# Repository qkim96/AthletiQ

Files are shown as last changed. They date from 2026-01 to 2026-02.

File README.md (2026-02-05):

# AthletiQ

## Table of Contents
<ul>
  <li>
    <a href="#project-overview">Project Overview</a>
  </li><br>

  <li>
    <a href="#methodology">Methodology</a>
    <ul>
      <li><a href="#object-detection">Object Detection</a></li>
      <li><a href="#object-tracking">Object Tracking</a></li>
      <li><a href="#pose-detection">Pose Detection</a></li>
      <li><a href="#action-state-estimation">Action State Estimation</a></li>
      <li><a href="#camera-orientation--control">Camera Orientation & Control</a></li>
      <li><a href="#data-transmission">Data Transmission</a></li>
    </ul>
  </li><br>

  <li>
    <a href="#system-design">System Design</a>
    <ul>
      <li><a href="#hardware">Hardware</a></li>
      <li><a href="#functionality">Functionality</a></li>
      <li><a href="#communication">Communication</a></li>
    </ul>
  </li><br>

  <li>
    <a href="#installation--configuration">Installation & Configuration</a>
    <ul>
      <li><a href="#tested-environments">Tested Environments</a></li>
      <li><a href="#prerequisites">Prerequisites</a></li>
      <li><a href="#structure">Structure</a></li>
      <li><a href="#setup-raspberry-pi">Setup (Raspberry Pi)</a></li>
      <li><a href="#setup-mobile-device">Setup (Mobile Device)</a></li>
    </ul>
  </li><br>

  <li>
    <a href="#operating-instructions">Operating Instructions</a>
    <ul>
      <li><a href="#hardware-1">Hardware</a></li>
      <li><a href="#mobile-device">Mobile Device</a></li>
    </ul>
  </li>
</ul>

<br><br>

---

## Project Overview
This project implements an autonomous, real-time basketball shooting capture and analysis system.

A motorized camera mounted on stationary device continuously tracks a player on the court, keeping the athlete centered in the frame during the play.
The system processes a live video feed to detect shooting events and automatically triggers recording when a shot occurs.
Each captured clip includes both the shooting action and a short temporal window preceding the event.
The system then analyzes the clip to extract the player’s shooting pose and relevant motion features, and packages the results alongside the recorded video.

The processed video and structured analysis data are transmitted to a server and displayed on a web interface, enabling remote visualization and performance review.
The design emphasizes real-time operation, autonomous capture, and seamless integration between on-device perception and web-based presentation.

<br>

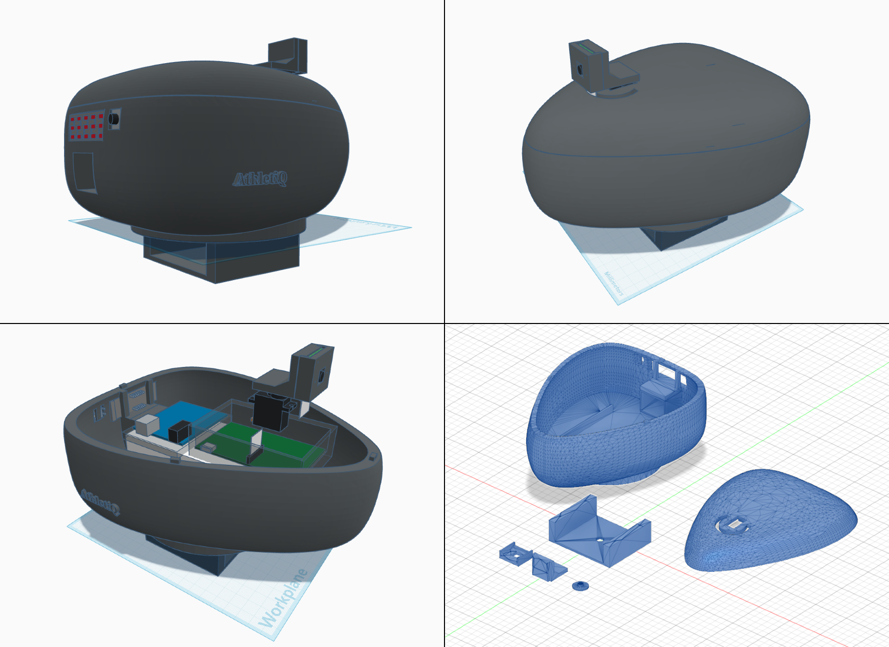
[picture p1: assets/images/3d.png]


<br>

---

## Methodology
This framework implements a real-time basketball action detection and pose analysis pipeline using probabilistic object localization/tracking algorithm and Bayesian state estimation model.  
<br>

### Object Detection
The basketball is detected using a binary mask generated via HSV thresholding, with selective pixel-level enhancement applied beforehand.
An enhancement mask is first computed in the LAB color space and used to boost pixel values only in regions likely to correspond to the ball, improving robustness to lighting variations.
HSV thresholding is then applied to produce the final detection mask, focusing the enhancement on the target object.

The detection mask is further discretized through morphological operations to separate undesired regions into smaller segments, enabling the selection of the most ball-like contour.
To improve stability, sudden jumps in the detected position (measurement noises) are filtered out before passing the measurement to the tracking stage.

<br>
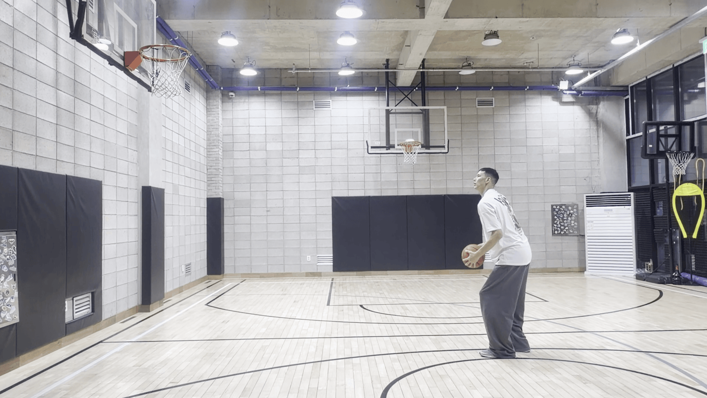
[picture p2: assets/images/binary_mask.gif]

<p align="center"><em>Visualization of the detection pipeline:<br>camera frame - LAB enhancement mask - final HSV detection mask</em></p>
<br>

### Object Tracking
The basketball is recursively localized and tracked from the camera live feed using a Kalman filter, which combines motion priors with noisy visual measurements.
This approach ensures robust tracking, even during occlusions, out-of-frame scenarios, and missed detections.  
<br>

The algorithm for Kalman filter is implemented as below,  
  
$`1: \hspace{1cm} {\bf Algorithm\hspace{6pt}KalmanFilter(}\mu_{t-1}, \Sigma_{t-1}, u_t, z_t{\bf ):}`$  
$`2: \hspace{2cm} \bar{\mu}_t = A_t \mu_{t-1} + B_t u_t`$  
$`3: \hspace{2cm} \bar{\Sigma}_t = A_t \Sigma_{t-1} A^T_t + R_t`$  
$`4: \hspace{2cm} K_t = \bar{\Sigma}_t C^T_t (C_t \bar{\Sigma}_t C^T_t + Q_t)^{-1}`$  
$`5: \hspace{2cm} \mu_t = \bar{\mu}_t + K_t (z_t - C_t \bar{\mu}_t)`$  
$`6: \hspace{2cm} \Sigma_t = (I - K_t C_t) \bar{\Sigma}_t`$  
$`7: \hspace{2cm} \text{return }\hspace{6pt}\mu_t\hspace{1pt}\text{, }\hspace{2pt}\Sigma_t`$

where the subscript $`(\cdot)_k`$ refers to the current state, $`(\cdot)_{k-1}`$ corresponds to the previous state, and a bar $`\bar{(\cdot)}`$ denotes the belief (a priori).  
<br>

The variables are defined as:

- $\mu$ :&nbsp;&nbsp;&nbsp;state estimate  
- $\Sigma$ :&nbsp;&nbsp;&nbsp;estimate covariance matrix  
- $u$ :&nbsp;&nbsp;&nbsp;control input  
- $z$ :&nbsp;&nbsp;&nbsp;measurement  
- $A$ :&nbsp;&nbsp;&nbsp;state transition model  
- $B$ :&nbsp;&nbsp;&nbsp;control input model  
- $R$ :&nbsp;&nbsp;&nbsp;process noise covariance matrix  
- $K$ :&nbsp;&nbsp;&nbsp;Kalman gain  
- $C$ :&nbsp;&nbsp;&nbsp;observation model
<br>

The Algorithm for the Kalman filter can be divided into two main steps: **prediction** and **update**.  
The prediction step occurs before the measurement is taken into account (lines 2–3 in the algorithm above).  
Lines 4–6 correspond to the update step, where the predicted current state is corrected after incorporating the measurement.  
With no measurement or control, the zero matrix $O$ can be used.

$`1: \hspace{1cm} {\bf Algorithm\hspace{6pt}KalmanFilter(}\mu_{t-1}, \Sigma_{t-1}, O, O{\bf ):}`$  
$`2: \hspace{2cm} \bar{\mu}_t = A_t \mu_{t-1} + B_t u_t = A_t \mu_{t-1} + B_t O = A_t \mu_{t-1}`$  
$`3: \hspace{2cm} \bar{\Sigma}_t = A_t \Sigma_{t-1} A^T_t + R_t`$  
$`4: \hspace{2cm} K_t = \bar{\Sigma}_t C^T_t (C_t \bar{\Sigma}_t C^T_t + Q_t)^{-1} = \bar{\Sigma}_t O^T (O \bar{\Sigma}_t O^T + O)^{-1} = O`$  
$`5: \hspace{2cm} \mu_t = \bar{\mu}_t + K_t (z_t - C_t \bar{\mu}_t) = \bar{\mu}_t + O (O - O \bar{\mu}_t) = \bar{\mu}_t`$  
$`6: \hspace{2cm} \Sigma_t = (I - K_t C_t) \bar{\Sigma}_t = (I - O O) \bar{\Sigma}_t = I \bar{\Sigma}_t = \bar{\Sigma}_t`$  
$`7: \hspace{2cm} \text{return }\hspace{6pt}\mu_t\hspace{1pt}\text{, }\hspace{2pt}\Sigma_t`$  
<br>

Simply,

$`1: \hspace{1cm} {\bf Algorithm\hspace{6pt}KalmanFilterPrediction(}\mu_{t-1}, \Sigma_{t-1}{\bf ):}`$  
$`2: \hspace{2cm} \bar{\mu}_t = A_t \mu_{t-1}`$  
$`3: \hspace{2cm} \bar{\Sigma}_t = A_t \Sigma_{t-1} A^T_t + R_t`$  
$`4: \hspace{2cm} \mu_t = \bar{\mu}_t`$  
$`5: \hspace{2cm} \Sigma_t = \bar{\Sigma}_t`$  
$`6: \hspace{2cm} \text{return }\hspace{6pt}\mu_t\hspace{1pt}\text{, }\hspace{2pt}\Sigma_t`$  
<br>

To implement the algorithm in practice, all parameters must be derived from the system dynamics.
Accordingly, the physics of a moving ball is modeled as follows.

The current state of a ball can be expressed in terms of the position, velocity, and acceleration.

$$
\begin{aligned}
p_t &= p_{t-1} + v_t \Delta t + \frac{1}{2} a_t \Delta t^2\\
v_t &= v_{t-1} + a_t \Delta t
\end{aligned}
$$

But since the frame of the camera video is in 2-dimension, each parameter can be split into x and y coordinates.

$$
\begin{alignedat}{2}
&x_t = x_{t-1} + v_{x,t} \Delta t + \frac{1}{2} a_{x,t} \Delta t^2 \hspace{1cm} &&y_t = y_{t-1} + v_{y,t} \Delta t + \frac{1}{2} a_{y,t} \Delta t^2\\
&v_{x,t} = v_{t-1} + a_t \Delta t \hspace{1cm} &&v_{y,t} = v_{t-1} + a_t \Delta t
\end{alignedat}
$$

And also note that $\Delta t$ is the difference between each frames (1 frame), which can be substituted as 1.  
Therefore all the parameters can be expressed as matrices.

$$
\mu_t = \begin{bmatrix}
x_t & y_t\\
v_{x,t} & v_{y,t}
\end{bmatrix} =
\begin{bmatrix}
1 & 1\\
0 & 1
\end{bmatrix}
\begin{bmatrix}
x_{t-1} & y_{t-1}\\
v_{x,t-1} & v_{y,t-1}
\end{bmatrix} +
\begin{bmatrix}
\frac{1}{2}\\
1
\end{bmatrix}
\begin{bmatrix}
a_{x,t-1} & a_{y,t-1}
\end{bmatrix}
$$

$$
A = \begin{bmatrix}
1 & 1\\
0 & 1
\end{bmatrix}
$$

$$
\epsilon_t = \begin{bmatrix}
\frac{1}{2}\\
1
\end{bmatrix}
\begin{bmatrix}
a_{x,t-1} & a_{y,t-1}
\end{bmatrix} = G A_t^T \sim \mathcal{N} (0, R_t)
$$

$$
G = \begin{bmatrix}
\frac{1}{2}\\
1
\end{bmatrix}
\hspace{1cm}
R_t = \sigma^2 G G^T = \begin{bmatrix}
0.25 & 0.5\\
0.5 & 1
\end{bmatrix}
$$

$$
Z_t = \begin{bmatrix}
x_t & y_t
\end{bmatrix} = C_t \mu_t + \delta_t
= \begin{bmatrix}
1 & 0
\end{bmatrix}
\begin{bmatrix}
x_t & y_t\\
v_{x,t} & v_{y,t}
\end{bmatrix} + \delta_t
$$

$$
C_t = \begin{bmatrix}
1 & 0
\end{bmatrix}
$$

Also, $\mu_t$ and $\Sigma_t$ at $t=0$ are set to a $2 \times 2\hspace{2pt}$ zero matrices.  

$$
\mu_0 = \begin{bmatrix}
0 & 0\\
0 & 0
\end{bmatrix}
\hspace{1cm}
\Sigma_0 = \begin{bmatrix}
0 & 0\\
0 & 0
\end{bmatrix}
$$

<br>

#### Applications of Kalman Filter to Handle Noisy Measurements
When detections are temporarily unavailable, the Kalman filter continues to predict the object’s location.
Once measurements become available again, the estimate is corrected using the new observations.
- **Green Circle:** measurement obtained from detection
- **Blue Circle:** Kalman filter prediction, with or without a valid detection

<br>
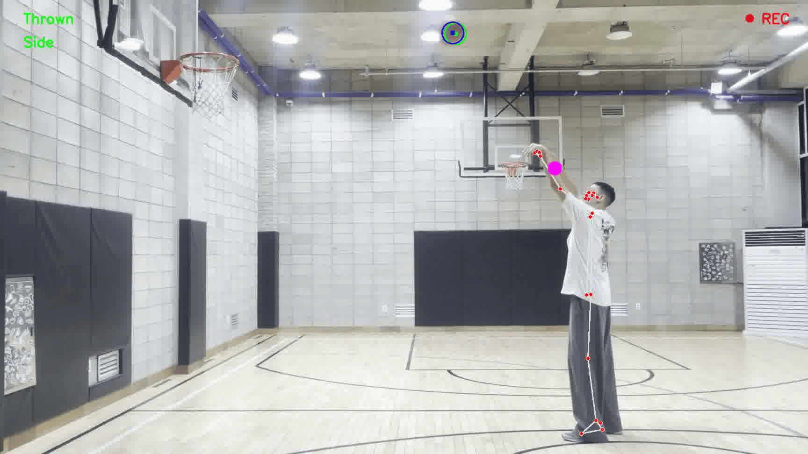
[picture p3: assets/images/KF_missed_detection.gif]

<p align="center"><em>Missed detection due to lighting conditions and motion blur</em></p>
<br>
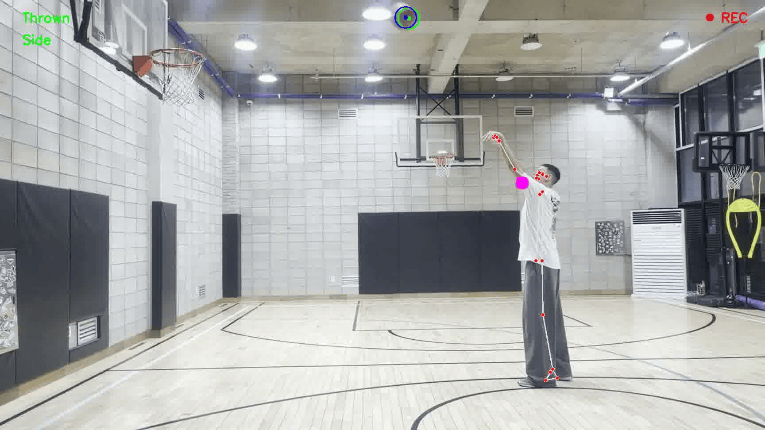
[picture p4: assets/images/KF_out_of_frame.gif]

<p align="center"><em>Missed detection due to object being out of frame</em></p>
<br>

### Pose Detection
Player pose landmarks are extracted from the video feed using MediaPipe Pose, which provides a set of 3D body keypoints of the detected player.
These landmarks include essential joints of a person, such as shoulders, elbows, wrists, hips, etc.

<p align="center">
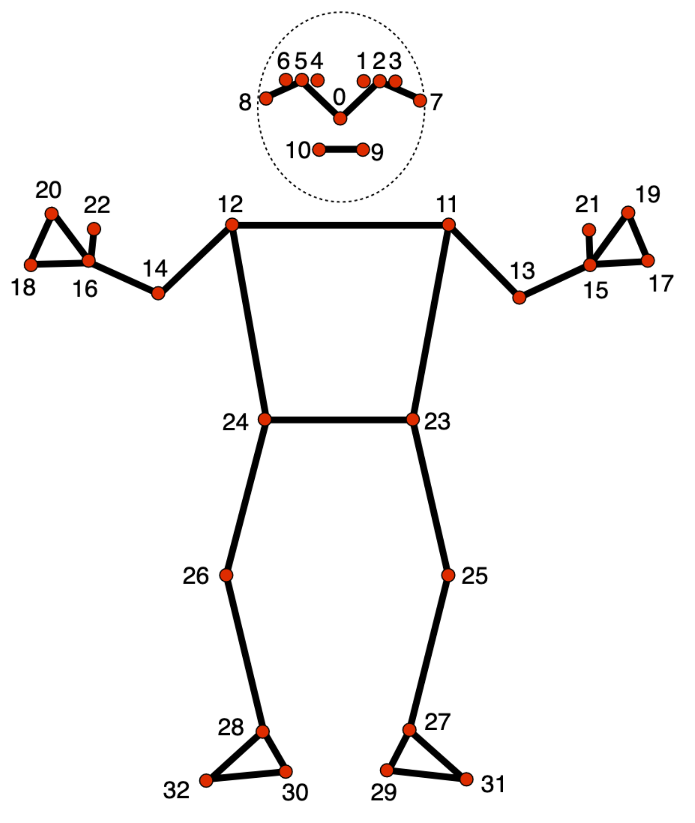
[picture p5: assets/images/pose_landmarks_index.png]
  
  <br>
  <em>MediaPipe pose landmarks</em>
</p>
<br>

### Action State Estimation
Shooting action recognition is formulated as a Hidden Markov Model with three hidden action states: 'Prep' ($\rho$), 'Set' ($\sigma$), and 'Thrown' ($\tau$).
Having binary observations and factorized features, the system uses a Bernoulli HMM with factorized emissions, and at each time step
(camera frame), online Bayesian filtering is performed via the HMM forward algorithm with a local Maximum a Posteriori (MAP) deterministic decision rule to infer the hidden states.
When the filtered posterior exhibits low confidence, a 1-step Viterbi-style local decoding  without backtracking is applied on the previously selected state to improve the consistency.

#### Hidden Markov Model Parameters
$`\mathcal{\lambda} \hspace{2pt} = \hspace{2pt} (\mathcal{S}, \mathcal{O}, \mathcal{\pi}, \mathcal{A}, \mathcal{B})`$  

- State Space:  
$`\mathcal{S} \hspace{2pt} = \hspace{2pt} \{\rho, \sigma, \tau\}`$

- Factorized Features:  
$`f_1, f_2, f_3 \hspace{2pt} \in \hspace{2pt} \{0,1\}`$

- Factorized Observation:  
$`\mathcal{O}' \hspace{2pt} = \hspace{2pt} (f_1, f_2, f_3)`$

- Observation Space:  
$`\mathcal{O} \hspace{2pt} = \hspace{2pt} \{\mathcal{O}' \hspace{4pt} | \hspace{4pt} f_k \in \{0,1\}, \quad k \in \{1,2,3\}\}`$

- Initial State Distribution:  
$`\pi \hspace{2pt} = \hspace{2pt} P(X_1 = s_i), \quad s_i \in \mathcal{S}, \quad i \in \{\rho, \sigma, \tau\}`$

- State Transition Model:  
$`\mathcal{A} \hspace{2pt} = \hspace{2pt} [a_{ij}], \quad a_{ij} \hspace{2pt} = \hspace{2pt} P(X_{t+1} = s_j \hspace{2pt} | \hspace{2pt} X_t = s_i), \quad i,j \in \{\rho, \sigma, \tau\}`$

- Factorized Emission Probability:  
$`\phi_{ik}(f_k) \hspace{2pt} = \hspace{2pt} Bernoulli(f_k \hspace{2pt} | \hspace{2pt} \theta_{ik}) \hspace{2pt} = \hspace{2pt} \theta_{ik}^{f_k}(1 - \theta_{ik})^{1-f_k}, \quad i \in \{\rho, \sigma, \tau\}, \quad k \in \{1,2,3\}`$

- Emission Probability Model:  
$`\mathcal{B} \hspace{2pt} = \hspace{2pt} [b_i(\mathcal{O}_t')], \quad b_i(\mathcal{O}_t') \hspace{2pt} = \hspace{2pt} P(\mathcal{O}_t' | X_t = s_i) \hspace{2pt} = \hspace{2pt} b_i(f_{1,t}, f_{2,t}, f_{3,t}) \hspace{6pt} =`$ $`\displaystyle \prod_{k=1}^{3}`$ $`\phi_{ik}(f_{k,t}), \quad i \in \{\rho, \sigma, \tau\}, \quad k \in \{1,2,3\}`$

<br>

#### Forward Algorithm Update
$`\alpha_1(j) \hspace{2pt} = \hspace{2pt} \pi_j \hspace{2pt}\cdot\hspace{2pt} \mathcal{B}_j(o_1)`$  

$`\alpha_t(j) \hspace{2pt} = \hspace{2pt} \mathcal{B}_j(o_t) \hspace{2pt}\cdot\hspace{2pt}`$ $`\displaystyle \sum_{i}^{\{\rho, \sigma, \tau\}}`$ $`\alpha_{t-1}(i) \hspace{2pt}\cdot\hspace{2pt} \mathcal{A}_{ij}`$  

#### Viterbi Algorithm Update
$`\delta_1(j) \hspace{2pt} = \hspace{2pt} \pi_j \hspace{2pt}\cdot\hspace{2pt} \mathcal{B}_j(o_1)`$  
$`\delta_t(j) \hspace{2pt} = \hspace{2pt} \mathcal{B}_j(o_t) \hspace{2pt}\cdot\hspace{2pt} \displaystyle \max_{i} [\delta_{t-1}(i) \hspace{2pt}\cdot\hspace{2pt} \mathcal{A}_{ij}]`$

#### State Selection
$`s_{\alpha, t} \hspace{2pt} = \hspace{2pt} \displaystyle \arg\max_j \alpha_t(j)`$  
$`s_{\delta, t} \hspace{2pt} = \hspace{2pt} \displaystyle \arg\max_j \delta_t(j)`$  

$`\displaystyle s_t =
\begin{cases}
s_{\alpha,t}, & \text{if confidence}_{\alpha,t} > \text{threshold} \\
s_{\delta,t}, & \text{otherwise}
\end{cases}
`$

<br>

### Camera Orientation & Control
Before starting the system, the user must place the device in either the front or side of the court, and press the push button to set the system mode (Front/Side) accordingly (shown on the hardware display).
In "Front mode", the camera is positioned directly under the basketball hoop facing the player to capture the shooting motion from the front, while in "Side mode", the camera is placed to the side of the player to capture the motion from a lateral perspective.
Camera orientation mode is determined by data received via UART serial communication and conditions the observation model.
The system also sends UART commands to rotate the camera when the player approaches the frame boundaries in order to constantly track and keep the player in frame.

<p align="center">
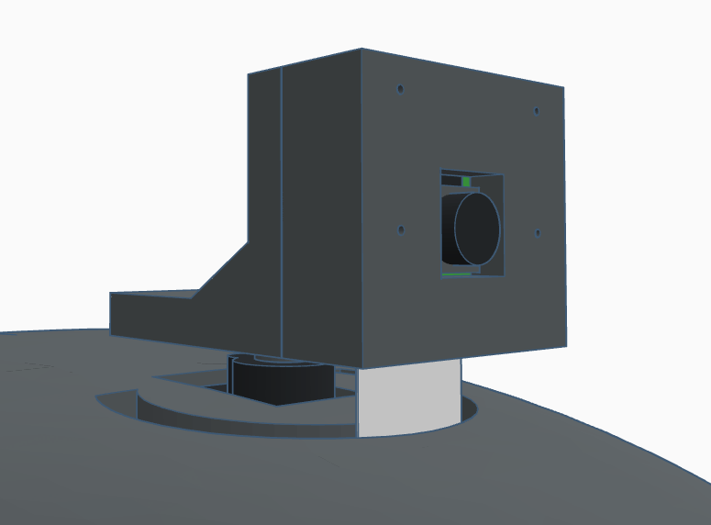
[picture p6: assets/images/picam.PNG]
  
  <br>
  <em>Motorized Raspberry Pi Camera mounted on the device</em>
</p>
<br>

### Data Transmission
Upon detecting a shooting action, the system automatically records a video clip, including a short buffer of preceding frames, which is then encoded into a H.264 format.
The player’s shooting pose is analyzed and the results are serialized to a JSON file.
Both the encoded video clip and the analyzed data are transmitted to the server for web-based visualization.

<br>

---

## System Design
### Hardware
* Raspberry Pi 4 Model B (8GB RAM)
* Raspberry Pi Camera Module V2
* Arduino Uno R3
* MG90S Servo Motor
* 5-Digit 7-Segment Display
* Push Button
* 5V 3A Power Source

### Functionality
* Raspberry Pi 4 + Camera Module V2:
  * Real-time video capture
  * Image processing
  * Object tracking and localization; pose analysis; state estimation
  * Data analysis and server transmission
* Arduino Uno:
  * Servo control
  * Display control
  * Push button input sensing
* 7-Segment Display:
  * Visual feedback of the current mode (Front/Side)
* Push button:
  * Manual switching between camera mode (Front/Side)
* Power Source:
  * Power Raspberry Pi, Arduino, and servo motor
  * Display remaining battery
  * Power button to turn on/off the entire system

### Communication
* UART Communication Protocol
  * Raspberry Pi sends a start sync byte to Arduino; Arduino waits to ensure Raspberry Pi is ready and Wi-Fi is connected.
  * Arduino sends an ACK byte to Raspberry Pi to confirm synchronized start.
  * Raspberry Pi sends left/right commands to Arduino to rotate camera when player is near frame boundaries.
  * Arduino sends the current mode (Front/Side) to Raspberry Pi by sensing push button input.
* Server Data Transmission
  * Raspberry Pi uploads recorded video clips (H.264) and analyzed data (JSON) to Firebase Cloud Storage.

<br>

---

## Installation & Configuration
### Tested Environments
* Raspberry Pi 4 Model B (8GB) - Bullseye OS
* Arduino Uno R3
* Ubuntu 22.04
* Windows 10
* iOS 16.3.1
* Android 9
* Termius 6.3.0

### Prerequisites
```
# Core packages (strict version constraints for compatibility)
python             >= 3.9, <= 3.10
mediapipe          >= 0.10.5, <= 0.10.11
protobuf           >= 3.11, < 4.0
numpy              >= 1.23, < 2.0
matplotlib         >= 3.7, < 3.10
opencv-python      >= 4.7, <= 4.12
firebase-admin     >= 5.0, < 6.0
absl-py            >= 1.0, < 2.0
attrs              >= 21.3

# Flexible packages (no strict version required)
imutils
simplejpeg
av
python-dotenv
pyserial
picamera2
```

### Structure
```
/etc/
├── xdg/lxsession/LXDE-pi/
│   └── autostart
└── wpa_supplicant/
    └── wpa_supplicant.conf

/usr/local/bin/
└── uid

{ABSOLUTE_PATH_TO}/AthletiQ/
├── .env
├── .uid
├── main.py
├── utils.py
├── camera_source.py
├── object_localization.py
├── pose_detection.py
├── state_estimation.py
├── video_encoding.py
├── data_extraction.py
├── data_serialization.py
├── server_publication.py
├── serial.communication.py
│
├── firebase/
│   ├── cred/
│   │   └── <FIREBASE_ACCOUNT_KEY>.json
│   ├── downloads/
│   │   └── 000000/
│   │       ├── front/
│   │       │   ├── front.h264
│   │       │   └── front.json
│   │       └── side/
│   │           ├── side.h264
│   │           └── side.json
│   └── json/
│       ├── AthletiQ_JSON_Schema.json
│       ├── sample_front.json
│       └── sample_side.json
│
└── log/
    ├── main.log
    └── system.log
```
<br>

### Setup (Raspberry Pi)
**1. Create directories**
```bash
mkdir AthletiQ git
```
<br>

**2. Clone this repository**
```bash
cd git
git clone https://github.com/qkim96/AthletiQ.git
```
<br>

**3. Edit the configuration files**
```bash
cd AthletiQ
```
- Change {ABSOLUTE_PATH_TO}/ to actual absolute path to the project directory "AthletiQ/" (/home/<user_name>/)
```bash
nano autostart
```
- Change <YOUR_WIFI_NAME> and <YOUR_WIFI_PASSWORD> to your Wi-Fi (mobile device hotspot recommended)
```bash
nano wpa_supplicant.conf
```
<br>

**4. Move the configuration files to the appropriate location**
```bash
sudo mv autostart /etc/xdg/lxsession/LXDE-pi/
sudo mv wpa_supplicant.conf /etc/wpa_supplicant/
```
<br>

**5. Edit the bash file, move the file to the appropriate location, and set executable permission**
- Change {ABSOLUTE_PATH_TO}/ to actual absolute path to the project directory "AthletiQ/" (/home/<user_name>/)
```bash
nano uid
```
- Move the file
```bash
sudo mv uid /usr/local/bin
```
- Set executable permission
```bash
sudo chmod +x /usr/local/bin/uid
```
<br>

**6. Move all core files (including the hidden files) to the project directory**
```bash
mv src/main_code/AthletiQ_Pi/* src/main_code/AthletiQ_Pi/.* /home/<user_name>/AthletiQ/
```
<br>

**7. Download Firebase account key to /home/<user_name>/AthletiQ/firebase/cred/**
- Go to Firebase Console
- Select your project
- Go to service account (in project settings gear icon)
- Click "Generate new private key"
- Move the file to "/home/<user_name>/AthletiQ/firebase/cred/"
<br>

**8. Edit the environment variables file**
- Change {ABSOLUTE_PATH_TO}/ to actual absolute path to the project directory "AthletiQ/" (/home/<user_name>/)
- Change {FIREBASE_ACCOUNT_KEY} to the downloaded Firebase account key file name
- Change {FIREBASE_STORAGE_BUCKET_ID} to your Firebase storage bucket ID
```bash
cd /home/<user_name>/AthletiQ/
nano .env
```
<br>

### Setup (Mobile Device)
1. Install "Termius" app (from App Store, Google Play Store, etc.)
2. Login with Google, Apple account, etc.
3. Set password

<br>

---

## Operating Instructions
### Hardware
1. Turn on the device with the power button.
2. Wait for the display to show the current mode.

### Mobile Device
*Repeat the following steps when switching users*  

3. Open Termius app.
4. Select "Connections" tab at the bottom.
5. Search "ssh <rpi_username>@<rpi_hostname>.local" (or select recent connection).
6. Enter Raspberry Pi password.
7. Type "uid ######" (6-digit user ID from the web for "######").
8. Ready to use.

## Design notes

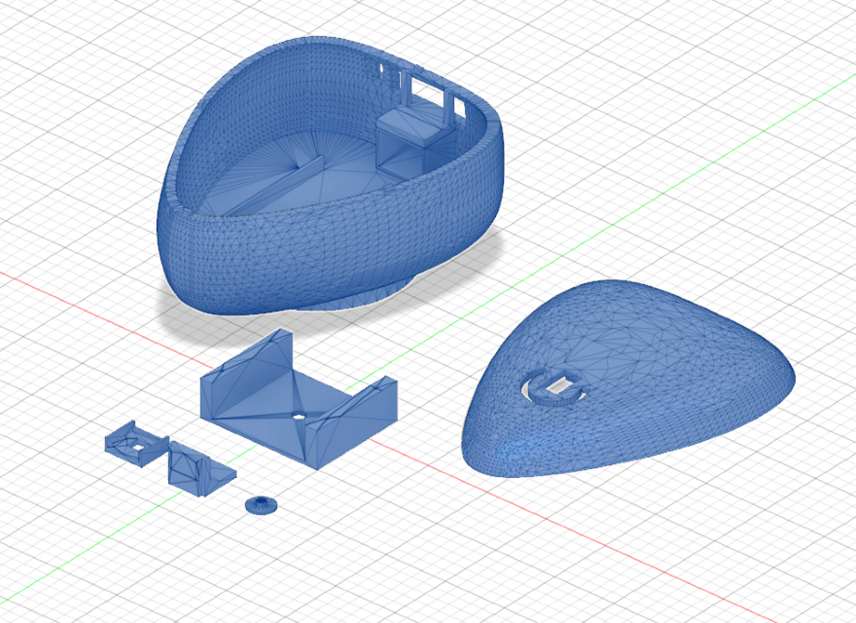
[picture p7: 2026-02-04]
assets/images/3d_4.png

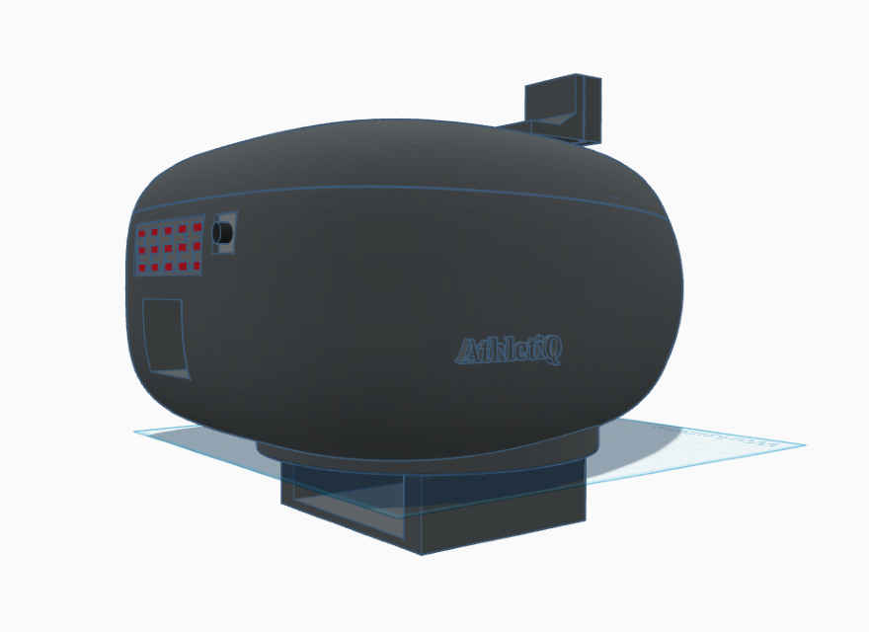
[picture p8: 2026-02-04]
assets/images/3d_1.png

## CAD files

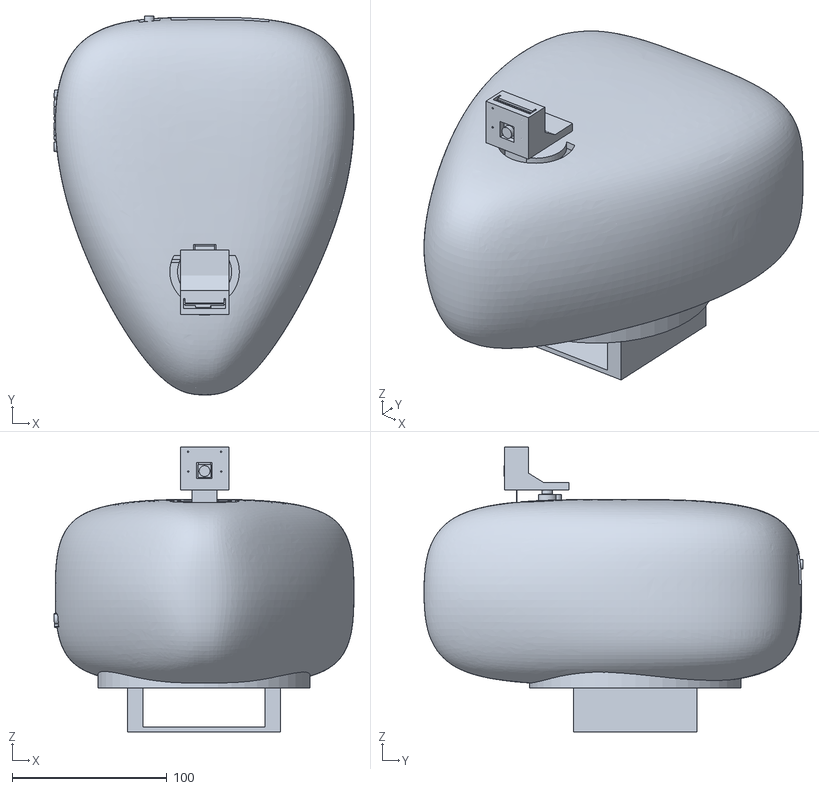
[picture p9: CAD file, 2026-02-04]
models/AthletiQ_assembled.stl
194.0 x 245.3 x 184.3

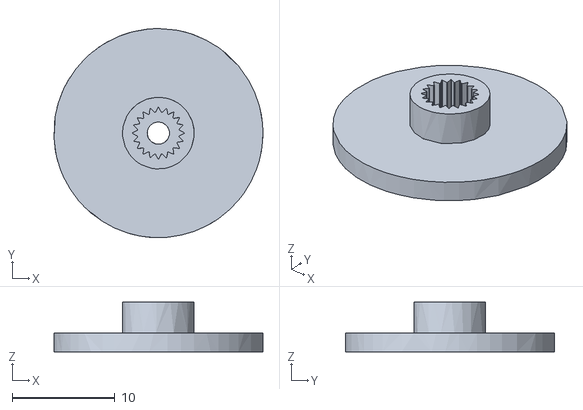
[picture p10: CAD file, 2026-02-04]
models/AthletiQ_parts05.stl
20.4 x 20.4 x 4.85

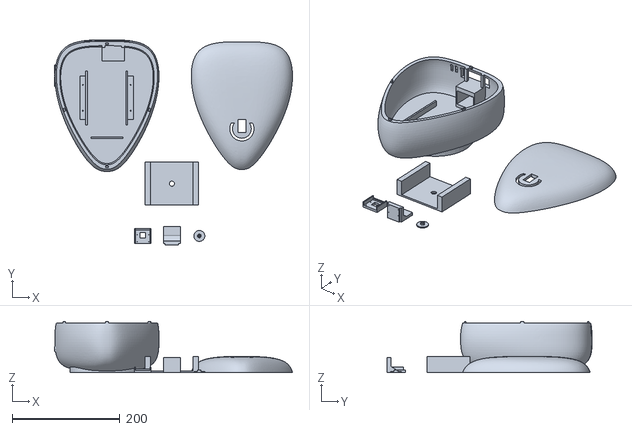
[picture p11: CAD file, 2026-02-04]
models/AthletiQ_parts.stl
442.0 x 381.3 x 94.9

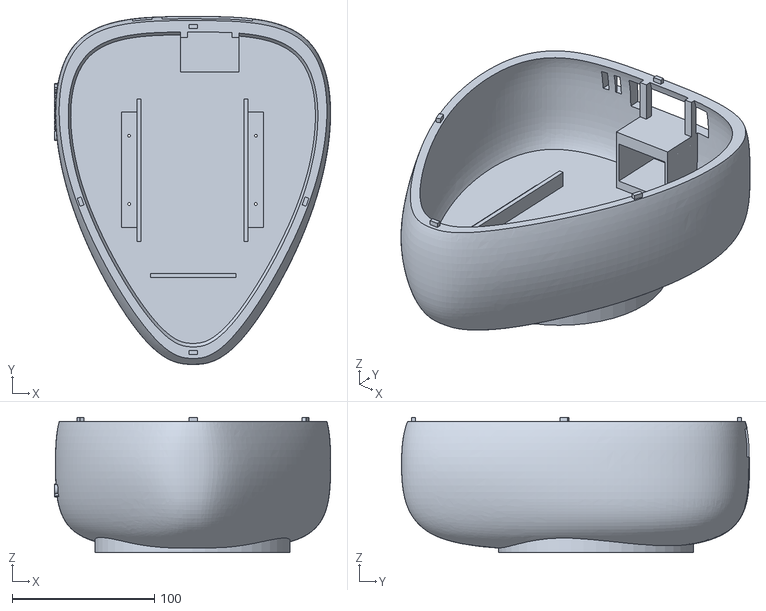
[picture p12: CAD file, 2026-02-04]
models/AthletiQ_parts01.stl
194.0 x 244.4 x 94.9

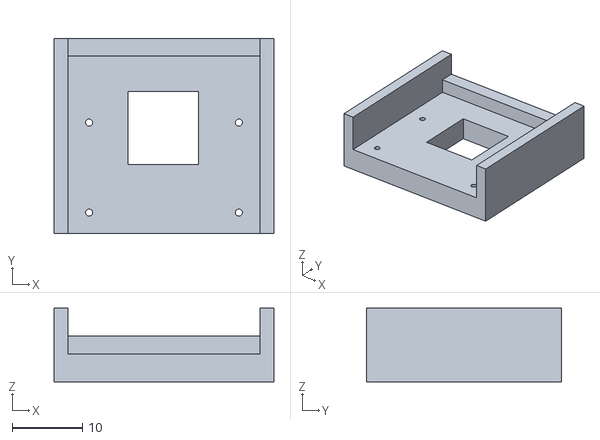
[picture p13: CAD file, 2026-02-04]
models/AthletiQ_parts04.stl
31.3 x 27.8 x 10.5

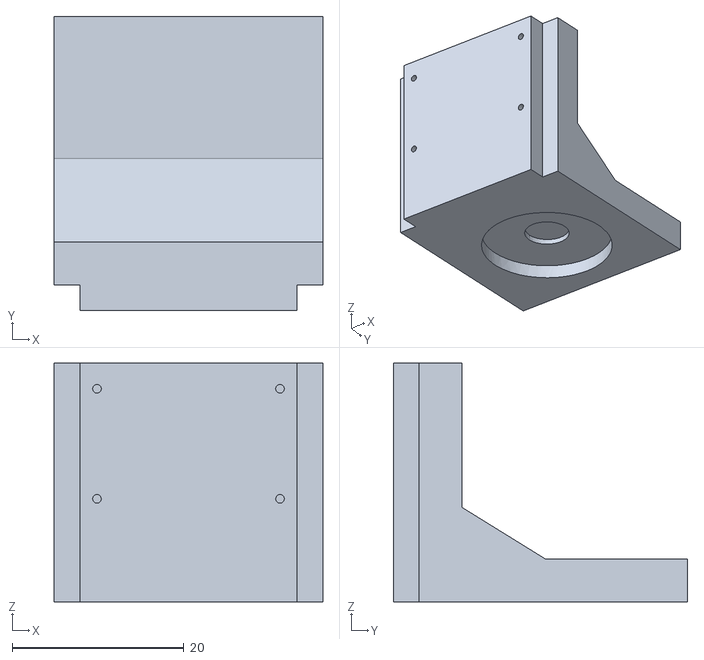
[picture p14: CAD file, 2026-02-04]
models/AthletiQ_parts03.stl
31.3 x 34.2 x 27.8

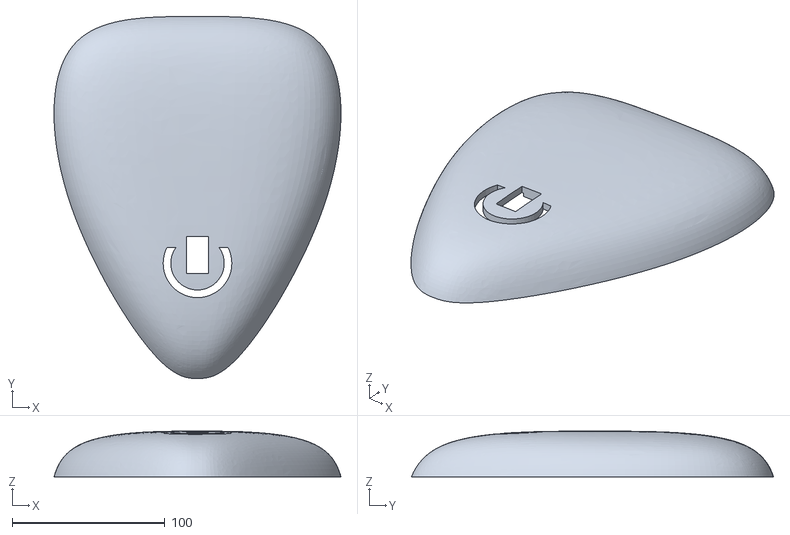
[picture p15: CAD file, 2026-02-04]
models/AthletiQ_parts02.stl
188.1 x 237.3 x 30.0

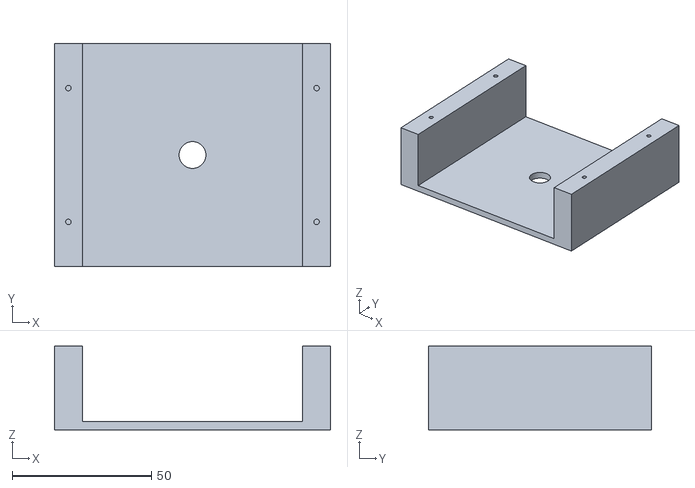
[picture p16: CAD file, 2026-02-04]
models/AthletiQ_parts06.stl
99.0 x 80.0 x 30.0

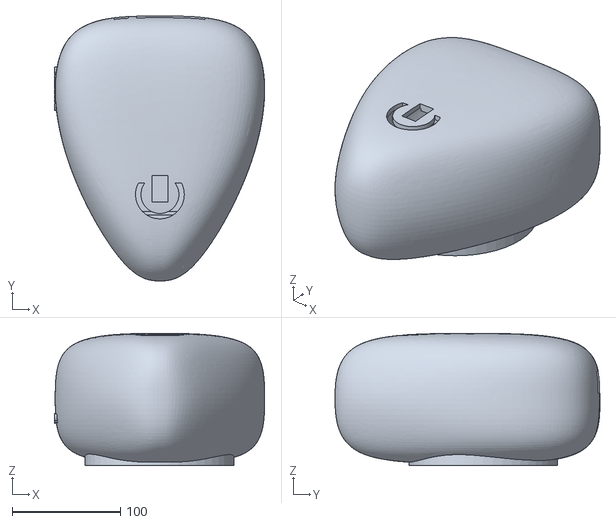
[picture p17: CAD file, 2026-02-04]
models/AthletiQ.stl
194.0 x 244.4 x 122.0

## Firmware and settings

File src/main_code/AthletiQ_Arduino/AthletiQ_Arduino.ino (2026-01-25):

#include <Servo.h>

// ------------------------------------------------------------------------------------------------------------
// VARIABLES
// ------------------------------------------------------------------------------------------------------------

// --- Global Time ---
unsigned long currentTime = 0;

// --- Pins ---
const int segPins[8] = {7, 3, A3, A1, A0, 6, A4, A2};  // A-DP pins
const int digitPins[5] = {8, 5, 4, A5, 2};             // Digit 1-5 pins
const int servoPin = 9;                                // Servo control pin
const int buttonPin = 13;                              // Button pin

// --- Button Debouncing Variables ---
const int debounceDelay = 50;                          // Time the input must remain stable to "trust" it
unsigned long lastDebounceTime = 0;                    // Last time the input has been changed

// --- Multiplex Display Variables ---
const int freq = 100;                                  // Multiplex refresh rate (Hz)
const int multiplexDelay = 1000 / (freq * 5);          // Delay for each digit's display "on" time (ms)
unsigned long lastDisplayTime = 0;                     // Last time when all the digits were displayed
int currentDigit = 0;                                  // Current digit to display (0-4)

// --- Servo Control Variables ---
Servo camServo;                                        // Servo object
unsigned int servoPos = 84;                            // Current servo position (initially at 84 degrees)
const int stepDelay = 10;                              // Delay between servo steps
const int stepSize = 3;                                // Degrees to rotate per step
unsigned long lastServoStepTime = 0;                   // Last time when the servo was rotated

// --- Booleans ---
bool prevReading = LOW;                                // Actual voltage reading (previous)
bool currReading = LOW;                                // Actual voltage reading (current)
bool confirmedBState = LOW;                            // Confirmed button state (pressed / not pressed)
bool isFront = false;                                  // Boolean representing the current mode
bool wifiConnected = false;                            // Boolean to indicate WiFi connection at Pi

// --- Display Alphabet Bytes ---
const byte alphabets[15] =                             // Byte data for each 7-segment alphabets
{                                                      // for common anode 5 digit display
  B10001110,  // F                                     // (bit order: DP-A)
  B10101111,  // r
  B10100011,  // o
  B10101011,  // n
  B10000111,  // t

  B10010010,  // S
  B11111001,  // i
  B10100001,  // d
  B10000110,  // E
  B11111111,  // blank

  B01111111,  // .
  B01111111,  // .
  B01111111,  // .
  B01111111,  // .
  B01111111   // .
};


// ------------------------------------------------------------------------------------------------------------
// UART RX Function:
// return the most recent byte received via UART
// ------------------------------------------------------------------------------------------------------------
char receiveData() {
  int byte_num = Serial.available();
  char rxData;

  for (int i = 0; i < byte_num; i++) {
    rxData = Serial.read();
  }

  return rxData;
}


// ------------------------------------------------------------------------------------------------------------
// Button Debounce Function:
// returns TRUE only on a confirmed button press/release
// ------------------------------------------------------------------------------------------------------------
bool buttonPressed()
{
  currReading = digitalRead(buttonPin);

  // If voltage reading is changed (including bouncing),
  if (currReading != prevReading) {
    lastDebounceTime = currentTime;        // reset the debounce timer.
  }

  // If voltage is stable enough (over delay threshold),
  if ((currentTime - lastDebounceTime) > debounceDelay) {

    if (currReading != confirmedBState) {  // check change in button state,
      confirmedBState = currReading;       // then finally update button state.

      // Detect confirmed button "press" (HIGH) / "release" (LOW)
      if (confirmedBState == HIGH) {
        prevReading = currReading;
        return true;
      }
    }
  }

  // Button press not detected
  prevReading = currReading;
  return false;
}


// ------------------------------------------------------------------------------------------------------------
// Multiplex Display Function:
// display a word (front/side), or "....." (dots) when Raspberry Pi is not connected to WiFi
// ------------------------------------------------------------------------------------------------------------
void updateDisplay(bool showFront, bool noWifi=false)
{
  // Delay for the display "on" time for each digit to visibly flicker (100Hz)
  if (currentTime - lastDisplayTime >= multiplexDelay) {
    // Turn off all digits
    for (int d = 0; d < 5; d++) digitalWrite(digitPins[d], LOW);

    // Select a starting byte to choose a word to display
    byte currAlph;
    if (noWifi) {
      // Select a byte to display "....." (dots)
      currAlph = alphabets[currentDigit+10];
    }
    else {
      // Select an alphabet to display, depending on the mode (front/side)
      currAlph = showFront ? alphabets[currentDigit] : alphabets[currentDigit+5];
    }

    // Set segments to display the selected alphabet
    for (int s = 0; s < 8; s++) digitalWrite(segPins[s], bitRead(currAlph, s));

    // Turn on the current digit
    digitalWrite(digitPins[currentDigit], HIGH);

    // Move to next digit
    currentDigit = (currentDigit + 1) % 5;

    // Update last display time
    lastDisplayTime = currentTime;
  }
}


// ------------------------------------------------------------------------------------------------------------
// Servo Control Function:
// rotate servo to the left/right depending on the received serial data from Raspberry Pi
// ------------------------------------------------------------------------------------------------------------
void updateServo(char rotateDir)
{
  // Delay for the servo control to slow down the rotation
  if (currentTime - lastServoStepTime >= stepDelay) {

    // Rotate left
    if (rotateDir == 'l') {
      servoPos -= stepSize;
      if (servoPos < 0) servoPos = 0;
    }

    // Rotate right
    else if (rotateDir == 'r') {
      servoPos += stepSize;
      if (servoPos > 180) servoPos = 180;
    }

    // Update the servo position and the timing variable
    camServo.write(servoPos);
    lastServoStepTime = currentTime;
  }
}


// ------------------------------------------------------------------------------------------------------------


void setup()
{
  Serial.begin(230400);

  pinMode(buttonPin, INPUT_PULLUP);   // initialize button pin as input

  for (int i = 0; i < 8; i++) {
    pinMode(segPins[i], OUTPUT);      // initialize segment pins as outputs
    digitalWrite(segPins[i], LOW);    // turn off all segment pins
  }

  for (int j = 0; j < 5; j++) {
    pinMode(digitPins[j], OUTPUT);    // initialize digit pins as outputs
    digitalWrite(digitPins[j], LOW);  // turn off all digit pins
  }

  camServo.attach(servoPin);          // attach servo pin to the servo
  camServo.write(servoPos);           // set servo to initial position
}



// ------------------------------------------------------------------------------------------------------------


void loop()
{
  // Current time
  currentTime = millis();
  
  // Blocking code to wait for Raspberry Pi to be connected to WiFi
  if (!wifiConnected) {
    updateDisplay(isFront, true);

    // Perform an initial startup handshake
    if (Serial.available() > 0) {
      byte rxByte = receiveData();
      if (rxByte == 0x55) {   // wait for start byte
        delay(2000);
        Serial.write(0xAA);   // send ACK byte
        wifiConnected = true;
      }
    }
    return;
  }

  // Detect a button press
  if (buttonPressed()) {
    isFront = !isFront;
    Serial.write(isFront ? '1' : '0');
  }

  // Update the display
  updateDisplay(isFront);

  // Receive serial data via UART to control servo
  if (Serial.available() > 0) {
    char rxData = receiveData();  // Receive serial data ('l' or 'r')
    updateServo(rxData);          // Update servo position
  }
}

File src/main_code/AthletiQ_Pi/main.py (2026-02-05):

#!/usr/bin/env python3

"""
This framework implements a real-time basketball action detection and pose analysis pipeline
using probabilistic object localization/tracking algorithm and Bayesian state estimation model.

A Kalman filter is used to recursively localize and track the basketball from a camera live
feed, combining motion priors with noisy visual measurements to remain robust to occlusions
and missed detections. Player pose landmarks are extracted using MediaPipe and fused with the
estimated position of the ball to construct binary observation features for action analysis.

Shooting action recognition is formulated as a Hidden Markov Model with three hidden action
states: 'Prep' (ρ), 'Set' (σ), and 'Thrown' (τ). Having binary observations and factorized
features, the system uses a Bernoulli HMM with factorized emissions, and at each time step
(camera frame), online Bayesian filtering is performed via the HMM forward algorithm with
a local Maximum a Posteriori (MAP) deterministic decision rule to infer the hidden states.
When the filtered posterior exhibits low confidence, a 1-step Viterbi-style local decoding
without backtracking is applied on the previously selected state to improve the consistency.

Camera orientation (front/side) is determined by data received via UART serial communication
from an Arduino and conditions the observation model. The system also sends UART commands to
rotate the camera when the player approaches the frame boundaries. Upon detecting a shooting
action, the system automatically records a video clip, combines past frames using a buffer,
analyzes the shooting pose, serializes results to JSON, and transmits H.264-formatted video
clip and JSON file containing the analyzed pose data to a server for web-based visualization.
"""


import utils
from utils import *
from camera_source import CameraSource
from object_localization import ObjectLocalizer
from pose_detection import PoseDetector
from state_estimation import StateEstimator
from video_encoding import VideoEncoder
from data_extraction import DataExtractor
from data_serialization import DataSerializer
from server_publication import ServerPublisher
from serial_communication import SerialCommunicator


def run():
    pub = ServerPublisher(firebase_cred_path=FIREBASE_CRED_PATH, firebase_storage_bucket=FIREBASE_STORAGE_BUCKET)
    SC.comm_init(port, baud)

    cam = CameraSource(platform="pi", src=0, rate=fps, size=res)
    cam.initialize()
    cam.start()

    time.sleep(2.0)

    while True:
        try:
            socket.create_connection(("8.8.8.8", 53), timeout=1)
            print("WiFi Connected")
            break
        except OSError:
            print("Waiting for WiFi...")
            time.sleep(1.0)

    SC.transmit_uart(sync_start=True)
    print("Start byte sent")

    while True:
        rxByte = SC.receive_uart()

        if rxByte == b'\xAA':
            print("Received ACK byte")
            break

        print("Waiting for ACK byte...")
        time.sleep(1.0)

    while True:
        loop_start_t = time.time()
        frame = cam.read()

        if frame is None:
            logging.warning("No frame received from camera")
            break
        if cv2.waitKey(1) & 0xFF == ord("q"):
            break

        frame = cv2.flip(frame, 1)

        c_measured, c_posteriori, r = OL.process_frame(frame)
        results, coords = PD.process_frame(frame)

        SE.observe(c_posteriori, r, coords)
        SE.estimate()

        filetime = datetime.now().strftime('%Y%m%d_%H%M%S')
        clip_ready = False
        clip_success = False
        json_success = False

        h264_bytes, timestamps = VE.update_buffer(frame, SE.s_t, SE.s_prev)

        if h264_bytes:
            clip_ready = True
            clip_filename = f'{filetime}.h264'

        if time.time() - VE.finalized_time >= past_t:
            data_ready =\
                DE.extract_data(
                    frame,
                    clip_ready,
                    VE.is_recording,
                    VE.is_in_action,
                    timestamps,
                    utils.mode_idx,
                    c_posteriori,
                    results
                )
        else:
            data_ready = False

        if data_ready:
            dict_data = DS.to_dict(DE)
            json_data = DS.to_json(dict_data)
            json_filename = f'{filetime}.json'

            if upload_files:
                json_success = \
                    pub.upload_file(
                        data_bytes=json_data,
                        remote_path=f'{DE.uid}/{filetime}/{json_filename}',
                        content_type='application/json'
                    )

            if save_files:
                with open(json_filename, "w", encoding="utf-8") as f:
                    f.write(json_data)
                print(f"Saved json: {json_filename}")

            if clip_ready:
                if upload_files:
                    clip_success = \
                        pub.upload_file(
                            data_bytes=h264_bytes,
                            remote_path=f'{DE.uid}/{filetime}/{clip_filename}',
                            content_type='video/h264'
                        )

                if save_files:
                    with open(clip_filename, "wb") as f:
                        f.write(h264_bytes)
                    print(f"Saved clip: {clip_filename}")

            VE.finalized_time = time.time()
            DE.clear_data()

        if clip_success and json_success:
            print(f"Successfully uploaded files {clip_filename} and {json_filename} to Firebase Storage")

        rotateL, rotateR = PD.body_position_LR(frame, coords)
        tx_data = SC.transmit_uart(rotateL, rotateR)
        rx_data = SC.receive_uart()

        if tx_data:
            print("UART Data Transmitted: ", tx_data)
        if rx_data and not VE.is_recording:
            utils.mode_idx = int(rx_data)

        frame_view = frame.copy()
        frame_view = draw_circles(frame_view, c_measured, c_posteriori, r)
        frame_view = draw_landmarks(frame_view, PD, results, coords)
        frame_view = draw_text(frame_view, SE.s_t, modes[utils.mode_idx])
        frame_view = draw_rec(frame_view, VE.is_recording)

        cv2.imshow("AthletiQ", frame_view)
        time.sleep(max((1. / computation_rate) - (time.time() - loop_start_t), 0))

    PD.release()
    cam.stop()
    cv2.destroyAllWindows()


if __name__ == "__main__":
    init_logger(LOG_FILE_PATH)

    OL = ObjectLocalizer()
    PD = PoseDetector()
    SE = StateEstimator()
    VE = VideoEncoder()
    DE = DataExtractor()
    DS = DataSerializer()
    SC = SerialCommunicator()

    run()

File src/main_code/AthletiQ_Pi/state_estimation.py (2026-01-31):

from utils import *


class StateEstimator:
    """
    Uses a Hidden Markov Model (HMM) with factorized geometric features derived
    from ball position and pose landmarks to estimates the current action state
    from visual observations.

    HMM forward filtering and 1-step Viterbi-style local decoding are combined
    with Maximum a Posteriori (MAP) deterministic decision rule to produce a
    stable estimate of the hidden state over time.

    Attributes
    ----------
    s_t : int or None
        Estimated current state index.
    o_t : str or None
        Current observation encoded as a binary feature string.
    s_prev : int or None
        Estimated previous state index.
    pi : numpy.ndarray
        Initial state distribution.
    A : numpy.ndarray
        State transition probability matrix.
    factorized_B : numpy.ndarray
        Factorized emission probability matrix.
    B : numpy.ndarray
        Emission probability matrix.
    alpha_t : numpy.ndarray or None
        Forward variable vector.
    delta_t : numpy.ndarray or None
        Viterbi log-probability vector.
    alpha_conf : float or None
        Confidence score for forward filtering.
    """

    def __init__(self):
        """
        Initializes the StateEstimator instance and all HMM parameters.

        Sets up state, observation, transition probabilities and emission
        probabilities derived from factorized features, and initializes
        forward and Viterbi variables.
        """

        self.s_t = None
        self.o_t = None
        self.s_prev = None

        self.pi = np.array([0.85, 0.1, 0.05])

        self.A = np.array([
            [0.90, 0.10, 0.00],
            [0.05, 0.20, 0.75],
            [0.30, 0.05, 0.65]
        ])

        self.factorized_B = np.array([
            [0.20, 0.05, 0.60],
            [0.90, 0.90, 0.90],
            [0.80, 0.45, 0.05]
        ])

        self.B = self.init_emission(self.factorized_B)

        self.alpha_t = None
        self.delta_t = None
        self.alpha_conf = None

    @staticmethod
    def init_emission(factorized_B):
        """
        Builds the full emission probability matrix from factorized features.

        :param factorized_B: Probability of each feature being true per state.
        :type factorized_B: numpy.ndarray
        :return: Emission probability matrix.
        :rtype: numpy.ndarray
        """

        n_state = len(states)
        n_feature = factorized_B.shape[1]
        n_col = 2 ** n_feature

        B = np.zeros((n_state, n_col))

        for obs in range(n_col):  # for all possible observations (= 2^{number_of_factorized_features})
            bits = [int(bit) for bit in f"{obs:0{n_feature}b}"]  # all 3-bit T/F combinations

            for state in range(n_state):  # for each hidden state
                emis_prob = 1.0
                for feat in range(n_feature):  # for each factorized feature
                    p_true = factorized_B[state, feat]  # probability of a feature being true
                    emis_prob *= (p_true ** bits[feat]) * ((1 - p_true) ** (1 - bits[feat]))  # Bernoulli distribution

                B[state, obs] = emis_prob

        return B

    def observe(self, ball_pos, radius, coords):
        """
        Extracts binary geometric features from the ball and pose landmarks
        and encodes them as a 3-bit observation string for the HMM.

        :param ball_pos: (x, y) pixel coordinates of the ball.
        :type ball_pos: tuple[int, int]
        :param radius: Radius of the detected ball.
        :type radius: int
        :param coords: Pose landmarks pixel coordinates.
        :type coords: tuple[tuple[int, int], ...]
        :return: None
        """

        if not radius or not coords:
            self.o_t = None
            return

        (ball_x, ball_y) = ball_pos
        (nose_x, nose_y), *hands, _ = coords

        ball = np.array(ball_pos)
        dist_thresh = radius * 3

        # Factorized features as booleans
        feat0 = ball_y < nose_y
        feat1 = any(hand_y < nose_y for _, hand_y in hands)
        feat2 = any(np.linalg.norm(ball - np.array(hand)) < dist_thresh for hand in hands)

        # A set of features (booleans) encoded into an observation (binary string)
        self.o_t = f"{int(feat0)}{int(feat1)}{int(feat2)}"

    def update_forward(self):
        """
        Performs forward filtering and updates the forward variable
        probability vector for the current observation.

        :return: None
        """

        o_t_idx = int(self.o_t, 2)
        B_o_t = self.B[:, o_t_idx]

        # At t=0
        if self.alpha_t is None:
            self.alpha_t = B_o_t * self.pi
            self.s_prev = np.argmax(self.alpha_t)

        # At t>0
        else:
            alpha_prev = self.alpha_t.copy()
            self.alpha_t = B_o_t * (alpha_prev.dot(self.A))

        # Normalize to avoid underflow & compute confidence
        self.alpha_t /= np.sum(self.alpha_t)
        alpha_weighted = self.alpha_t * self.A[self.s_prev, :]
        self.alpha_conf = alpha_weighted[np.argmax(self.alpha_t)] / np.sum(alpha_weighted)

    def update_viterbi(self):
        """
        Performs Viterbi-style decoding and updates the Viterbi
        log-probability vector for the current observation.

        :return: None
        """

        o_t_idx = int(self.o_t, 2)
        B_o_t = self.B[:, o_t_idx]
        eps = 1e-12

        # At t=0
        if self.delta_t is None:
            self.delta_t = np.log(B_o_t + eps) + np.log(self.pi + eps)
            self.s_prev = np.argmax(self.delta_t)

        # At t>0
        else:
            # Normalize with log space to avoid underflow
            delta_prev = self.delta_t.copy()
            self.delta_t = (np.log(B_o_t + eps)
                            + np.max(delta_prev[:, None] + np.log(self.A + eps), axis=0)
                            + np.log(self.A[self.s_prev, :] + eps))

    def estimate(self):
        """
        Estimates the current hidden state using both Forward and Viterbi algorithms.

        Updates the hidden state at current time step `s_t` by choosing between the
        forward estimate and Viterbi estimate depending on the forward filtering
        confidence score.

        :return: None
        """

        if self.o_t is None:
            self.s_t = -1
            return

        self.s_prev = self.s_t

        # Update alpha/delta
        self.update_forward()
        self.update_viterbi()

        # State estimation using Forward/Viterbi algorithm
        s_bel_forward = np.argmax(self.alpha_t)
        s_bel_viterbi = np.argmax(self.delta_t)

        # State selection based on forward confidence
        if self.alpha_conf > 0.1:
            self.s_t = s_bel_forward
        else:
            self.s_t = s_bel_viterbi

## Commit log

2025-12-03 button debounce test code
2025-12-03 servo range test code
2025-12-03 switch words to display with a button push
2025-12-03 main code for Arduino
2025-12-18 test code for Kalman Filter detection & prediction
2025-12-18 UART test code
2026-01-22 Changed pins for circuit simplicity and flipped alphabet bits to match the common anode display
    [AthletiQ_Arduino.ino]
2026-01-22 Implemented UART communication
2026-01-24 Added a blocking code to wait for Raspberry Pi to be connected to WiFi
2026-01-25 Set servo initial position to the desired orientation
2026-01-27 Main code for Raspberry Pi
2026-02-01 Implemented LAB-based enhancement and noise (outlier) filtering
    [object_localization.py, utils.py]
2026-02-02 Sample JSON data
2026-02-04 3D models
    [AthletiQ.stl, AthletiQ_assembled.stl, AthletiQ_parts.stl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]
2026-02-04 Applications of Kalman filter images
2026-02-04 Applications of Kalman filter gif
